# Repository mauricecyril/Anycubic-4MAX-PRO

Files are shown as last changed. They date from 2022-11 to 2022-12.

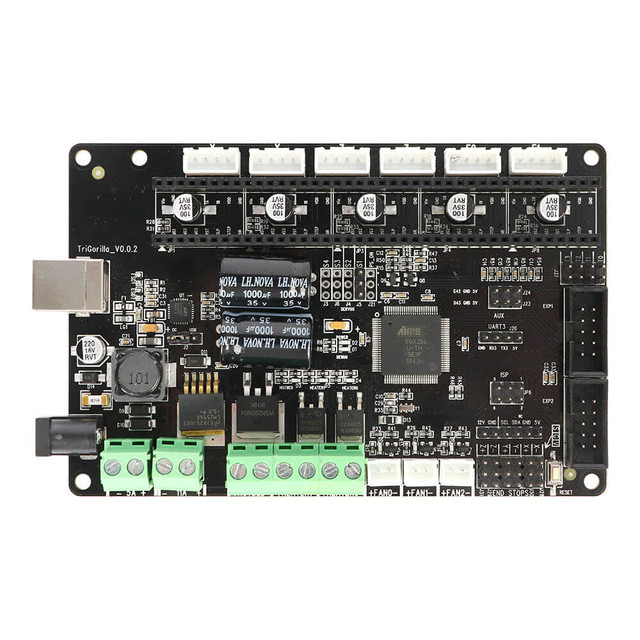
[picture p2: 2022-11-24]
references/anycubic-trigorilla-3d-printer-main-control-board-1000x1000__66155.jpg

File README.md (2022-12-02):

# Anycubic 4MAX PRO
Settings and Notes Related to the Anycubic 4Max Pro 3D Printer.

### **WARNING**: USE AT YOUR OWN RISK! All information collected on this github is for research purposes and is NOT professional advice or should not be considered a definative source for understanding, modifying or configuring the Anycubic 4Max Pro 3d printer or any 3d printer. Please do your own research and make sure you understand the potential risks, loss or damage to your health, your 3d printer, your house or those around you should you use the Anycubic 4Max Pro or follow or use any of the settings, files or information provided on this github repository. You assume all responsibility and liability for any damage or harm that may occur by following the information aggregated and posted here. USE AT YOUR OWN RISK!

## Information 
The heated bed of this printer tends to get warped and it becomes imposible to manually level the bed. The alternative is to add Mesh Leveling capabilities to this printer to make it usable.  

The printer uses a trigorilla board v1.0 but please double check by opening up the base of the printer and check the mainboard (see https://github.com/knutwurst/Marlin-2-0-x-Anycubic-i3-MEGA-S/wiki/Beginner's-Guide-(English)#3-identification-of-the-mainboard ) 

There is also a daughter board connected which has the pins for the end stops.

## Adding BL Touch to the Anycubic 4Max Pro V1.0
 **WARNING: USE AT YOUR OWN RISK! Please make sure to do your own configuration and conduct your own research before flashing your printers firmware, installing a BLTouch or configuring the BLtouch for the printer. I am not responsible for any potential risks, loss or damage to your health, your 3d printer, your house or those around you should you use the Anycubic 4Max Pro or follow or use any of the settings, files or information provided on this github repository. USE AT YOUR OWN RISK!**

### Purchase a genuine BLTouch
Try to acquire a genuine BLTouch device as there are reports of clones generally failing or having quality issues.
Make sure to also get the 1.5m extension wire with the dupont connectors.

The trigorilla mainboard on the Anycubic 4Max Pro has the servo control pins already soldered on
"+ - Power"
"- - GND"
"S - Signal"

But the BLTouch dupont connector needs to be reconfigured (see https://www.antclabs.com/wiring ) to swap the power and ground.
Original BLTouch Wiring 

| Original BLtouch Wiring | Modified BLtouch wiring | Connection to Anycubic 4MaxPro Boards |
| --- | --- |  --- |
| Brown (GND)  | Red (5V)  | + Servo Headers on Main Board |
| Red (5V)  | Brown (GND)  | - Servo Headers on Main Board |
| Orange (Signal)  | Orange (Signal)  | S Servo Headers on Main Board |
| Black (GND) | Black (GND)  | Black (GND) on Daughter board |
| White (Z axis Signal)  | White (Z axis Signal)  | White (Z axis Signal) on Daughter board  |

### Print a custom mount
Find a suitable BLtouch mount or experiment with one of the following:
| STL | Approximate Offset (Make sure to do your own calibration) | 
| --- | --- |
| Ancycubic 4MaxPro Standard Fan BLtouch Mount v4.stl | X Offset = +54.87mm, Y Offset = -1.70mm, Z Offset = |
| Ancycubic 4MaxPro Vortex Fan BLtouch Mount v2.stl | X Offset =+55.43mm , Y Offset =-2.0 (other readings say -7.91mm) , Z Offset = -3.58 or-3.52 (Probe extends 8.78mm - Distance from probe base to nozzle is 8.43mm). You might need to add a hex nut as a spacer to bring the probe lower. |

Make sure to calibrate the location of the BLTouch Probe in relation to your nozzle.

Remember the X,Y,Z are coordinates oriented when you're facing the front of the printer (ie. the door on the front of the 4Max Pro).
Y axis is the movement towards and away from you. So +Y is moving the printer head away from you, -Y is moving the printer head towards you.
X axis is the movement left and right of you. So +X is moving the printer head to the right, -X is moving the printer to the left.
Z axis is the movement up and down. So +Z is moving the pritner head up away from the printer bed, -Z is moving the printer down towards the printer bed.

### Flash the appropriate firmware (if required)
Knutwurst's i3 MEGA M/S/P/X/Chiron/4MP2 Hybrid Firmware (based on Marlin 2.1.x)
https://github.com/knutwurst/Marlin-2-0-x-Anycubic-i3-MEGA-S/releases

Make sure to compile your own version using the Arduino IDE and configure the X,Y,Z offsets! Make sure to follow the post firmware installation calibration steps. 

### Remove Bottom Cover
Lay the printer flat so that the bottom cover is exposed. To remove the base plate remove the four hex machine screws (M3x12) and also remove the padded covers and remove additional 4 machine hex screws (M4x8). 

### Remove Back Cover
Stand the printer back up (you can use the cover to protect the main board).
Remove the 8 screws on the back panel and remove the back panel to get run the extension cable through the existing cable management. You may want to add your own zip ties to anchor the new wires.

### Wire up the Extension Wire to the controller and daughter board
Lay the printer flat again (ie. front door laying flat).

# Ultimaker Cura 4.4 Settings for the Anycubic 4Max Pro
If "Origin at Center" is checked when slicing the printer seems to print off the printbed and in the lower left quadrant. Recommendation is to keep this setting unchecked. 

Settings / Printer / Manage Printers

Edit Machine Settings

Printer

    Printer Settings
    
        X (Width): 270mm
        Y (Depth): 205 mm
        Z (Height): 205 mm
        Build Plate Shape: Rectangular
        Origin at Center: Unchecked
        Heated Bed: Checked
        Heated Build Volume: Unchecked
        G-Code Flavor: Marlin
        
    Printhead Settings
        X min: 0
        Y min: 0
        X max: 205
        Y max: 205
        Gantry Height: 25.0
        Number of Extruders: 1
        
    Start G-Code
        G21 ;metric values
        G90 ;absolute positioning
        M82 ;set extruder to absolute mode
        M107 ;start with the fan off
        G28 X0 Y0 ;move X/Y to min endstops
        G28 Z0 ;move Z to min endstops
        G1 X-3 Y40 ;Anycubic 4Max Pro Brush
        G1 X-3 Y5 ;Anycubic 4Max Pro Brush
        G1 X-3 Y40 ;Anycubic 4Max Pro Brush
        G1 X-3 Y5 ;Anycubic 4Max Pro Brush
        G1 Z15.0 F{speed_travel} ;move the platform down 15mm
        G92 E0 ;zero the extruded length
        G1 F200 E3 ;extrude 3mm of feed stock
        G92 E0 ;zero the extruded length again
        G1 F{speed_travel}
        M117 Printing...
        G5

    End G-Code
        M104 S0 ; turn off extruder
        M140 S0 ; turn off bed
        M84 ; disable motors
        M107
        G91 ;relative positioning
        G1 E-1 F300 ;retract the filament a bit before lifting the nozzle, to release some of the pressure
        G1 Z+0.5 E-5 ;X-20 Y-20 F{speed_travel} ;move Z up a bit and retract filament even more
        G28 X0 ;Y0 ;move X/Y to min endstops, so the head is out of the way
        G1 Y180 F2000
        M84 ;steppers off
        G90
        M300 P300 S4000        

Extruder 1

    Nozzle Settings
    
        Nozzle Size: 0.4 mm
        Compatible Material Diameter: 1.75 mm
        Nozzle Offset X: 0 mm
        Nozzle Offset Y: 0 mm
        Cooling Fan Number: 0
        
    Extruder Start G-Code: Blank
    Extruder End G-Code: Blank
    
# Ultimaker Cura 4.4 Settings for the Anycubic 4Max Pro with BLTouch
If "Origin at Center" is checked when slicing the printer seems to print off the printbed and in the lower left quadrant. Recommendation is to keep this setting unchecked. Removed 

Settings / Printer / Manage Printers

Edit Machine Settings

Printer

    Printer Settings
    
        X (Width): 270mm
        Y (Depth): 205 mm
        Z (Height): 205 mm
        Build Plate Shape: Rectangular
        Origin at Center: Unchecked
        Heated Bed: Checked
        Heated Build Volume: Unchecked
        G-Code Flavor: Marlin
        
    Printhead Settings
        X min: 0
        Y min: 0
        X max: 205
        Y max: 205
        Gantry Height: 25.0
        Number of Extruders: 1
        
    Start G-Code
        G21 ;metric values
        G90 ;absolute positioning
        M82 ;set extruder to absolute mode
        M107 ;start with the fan off
        G28 X0 Y0 ;move X/Y to min endstops
        G28 Z0 ;move Z to min endstops
        G1 X-3 Y40 ;Anycubic 4Max Pro Brush
        G1 X-3 Y5 ;Anycubic 4Max Pro Brush
        G1 X-3 Y40 ;Anycubic 4Max Pro Brush
        G1 X-3 Y5 ;Anycubic 4Max Pro Brush
        G1 Z15.0 F{speed_travel} ;move the platform down 15mm
        G92 E0 ;zero the extruded length
        G1 F200 E3 ;extrude 3mm of feed stock
        G92 E0 ;zero the extruded length again
        G1 F{speed_travel}
        M117 Printing...
        G5

    End G-Code
        M104 S0 ; turn off extruder
        M140 S0 ; turn off bed
        M84 ; disable motors
        M107
        G91 ;relative positioning
        G1 E-1 F300 ;retract the filament a bit before lifting the nozzle, to release some of the pressure
        G1 Z+0.5 E-5 ;X-20 Y-20 F{speed_travel} ;move Z up a bit and retract filament even more
        G28 X0 ;Y0 ;move X/Y to min endstops, so the head is out of the way
        G1 Y180 F2000
        M84 ;steppers off
        G90
        M300 P300 S4000        

Extruder 1

    Nozzle Settings
    
        Nozzle Size: 0.4 mm
        Compatible Material Diameter: 1.75 mm
        Nozzle Offset X: 0 mm
        Nozzle Offset Y: 0 mm
        Cooling Fan Number: 0
        
    Extruder Start G-Code: Blank
    Extruder End G-Code: Blank

# Octoprint Settings
Still researching

# Sources

## Github
Knutwurst's i3 MEGA M/S/P/X/Chiron/4MP2 Hybrid Firmware (based on Marlin 2.1.x)
https://github.com/knutwurst/Marlin-2-0-x-Anycubic-i3-MEGA-S/releases

Marlin 2.0.x for Anycubic 4Max Pro [Does not compile in Arduino]
https://github.com/Poket-Jony/Marlin-A4MaxPro-2.0.x

## Thingiverse
Anycubic 4Max Pro Cable Chain by wadzio October 15, 2019
https://www.thingiverse.com/thing:3918237

Anycubic 4Max Pro Cable Chain - fixed parts by BgB42O June 14, 2020
https://www.thingiverse.com/thing:4459661

Vortex Fan Duct for Anycubic 4Max Pro by ontherunstudio July 26, 2019
https://www.thingiverse.com/thing:3772311

Anycubic 4Max Pro 2.0 Print head lid by alex_trask August 16, 2021
https://www.thingiverse.com/thing:4934115

4max pro Cura 4.1 profiles by skfinley July 29, 2019
https://www.thingiverse.com/thing:3778487

4Max Pro BLTouch Cable Holder by neutr0n January 07, 2020
https://www.thingiverse.com/thing:4090425

BLTouch and 3D Touch mount for Anycubic Mega S/X/P by Knutwurst October 25, 2021
https://www.thingiverse.com/thing:5030218

## Reddit
BLtouch on an Anycubic 4Max Pro by g8tto3
https://www.reddit.com/r/3Dprinting/comments/g8tto3/bltouch_on_an_anycubic_4max_pro/
https://web.archive.org/web/20221124154853/https://www.reddit.com/r/3Dprinting/comments/g8tto3/bltouch_on_an_anycubic_4max_pro/

BLTouch Installation (english) from Marlin-2-0-x-Anycubic-i3-MEGA-S
https://github.com/knutwurst/Marlin-2-0-x-Anycubic-i3-MEGA-S/wiki/BLTouch-Installation-(english)

Beginner's Guide (English) from Marlin-2-0-x-Anycubic-i3-MEGA-S
https://github.com/knutwurst/Marlin-2-0-x-Anycubic-i3-MEGA-S/wiki/Beginner's-Guide-(English)#3-identification-of-the-mainboard

Installed BLTouch last night. Here's things I wish I'd known.
https://www.reddit.com/r/ender3/comments/c6n02e/installed_bltouch_last_night_heres_things_i_wish/

Help me recognizing Trigorilla board versions
https://www.reddit.com/r/anycubic/comments/jns8l1/help_me_recognizing_trigorilla_board_versions/

## Other references
https://3dtoday.ru/blogs/darkcats/the-installation-of-the-level-sensor-table-bltouch3dtouch-and-clones-a

Camera Mounts to adapt:
https://www.thingiverse.com/thing:5147960

## Z - Offset Calibration
Source: https://github.com/knutwurst/Marlin-2-0-x-Anycubic-i3-MEGA-S/wiki/BLTouch-Installation-(english)
Also see: https://www.webcarpenter.com/blog/162-3D-Print---How-to-calibrate-Z-offset-with-a-BLTouch-bed-leveling-probe-sensor

Example:

Heat up the bed

G28

G90

G1 Z10

G1 X40 Y40 F4000

M280 P0 S10

G91

Slowly lower the nozzle with G1 Z-1 or G1 Z-0.1 or G1 Z-0.02 until the sensor is triggered. NOT FURTHER!

If the sensor has triggered and flashes: M280 P0 S160

M114 = Current position of the nozzle -> note! (e.g. Recv: X:40.00 Y:40.00 Z:1.30 E:0.00 Count X:3200 Y:3200 Z:520)

G90

G1 X38 Y15 F4000 (values from point 10 + offset of the sensor, i.e. X=40+(-2) and Y=40+(-25))

G91

Place a sheet of paper under the nozzle

Slowly lower the nozzle with G1 Z-1 or G1 Z-0.1 or G1 Z-0.02 until the paper is difficult to move.

M114 = Current position of the nozzle -> note! (e.g. Recv: X:38.00 Y:15.00 Z:0.70 E:0.00 Count X:3200 Y:3200 Z:520)

Subtract the Z value from point 16 from that from point 10 -> 1.30 - 0.7 = 0.6 mm -> This is our Z offset.

M851 Z-0.6 (be aware of the negative sign!)

M500

Carry out Autoleveling again via the display. Finished.

### Start G-Code - Cura
G21 ;metric values
G90 ;absolute positioning
M82 ;set extruder to absolute mode
M107 ;start with the fan off
M280 P0 S160 ; BLTouch alarm release
G4 P100 ; delay for BLTouch
G28 X0 Y0 ;move X/Y to min endstops
G28 Z0 ;move Z to min endstops
G28 ; home
G29 ; auto bed leveling
G1 X-3 Y40 ;Anycubic 4Max Pro Brush
G1 X-3 Y5 ;Anycubic 4Max Pro Brush
G1 X-3 Y40 ;Anycubic 4Max Pro Brush
G1 X-3 Y5 ;Anycubic 4Max Pro Brush
G1 Z15.0 F{speed_travel} ;move the platform down 15mm
G92 E0 ;zero the extruded length
G1 F200 E3 ;extrude 3mm of feed stock
G92 E0 ;zero the extruded length again
G1 F{speed_travel}
M117 Printing...
G5

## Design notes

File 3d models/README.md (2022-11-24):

# Slicer Settings

Use PETG or a heat resistant material. 

In tests, I've used Overture Black PETG and there was some stringing that needed cleaning up after. 

## Ultimaker Cura Settings

### Layer Height, Infill, Temp
Layer Height: 0.15mm

Infill Density: 100%

Print Temperature: 250.0 C

Build Plate Temperature: 70.0 C

### Cooling
Enable Print Cooling: No

Regular/Maximum Fan Speet Threshold: 10%

Regular Fan Speed at Height: 0.3mm

Regular Fan Speed at Layer: 2

Minimum Layer Time: 5.0s

Minimum Speed: 10.0 mm/s

Lift Head: No

### Supports
Generate Supports: Yes

Support Structure: Normal

Support Placement: Touching Buildplate

Support Overhang Angle: 50%

Support Pattern: Lines

Support Density: 15%

### Adhesion
Build Plate Adhesion: Yes

Build Plate Adhesion Type: Skirt

Skirt Line Couunt: 1

Skirt Distance 3.0mm

Skirt/Brim Minimum Length: 250.0mm

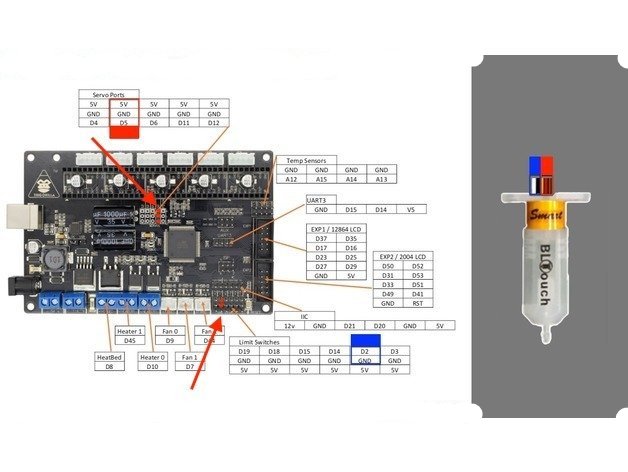
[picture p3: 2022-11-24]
references/trigorilla board bltouch.jpg

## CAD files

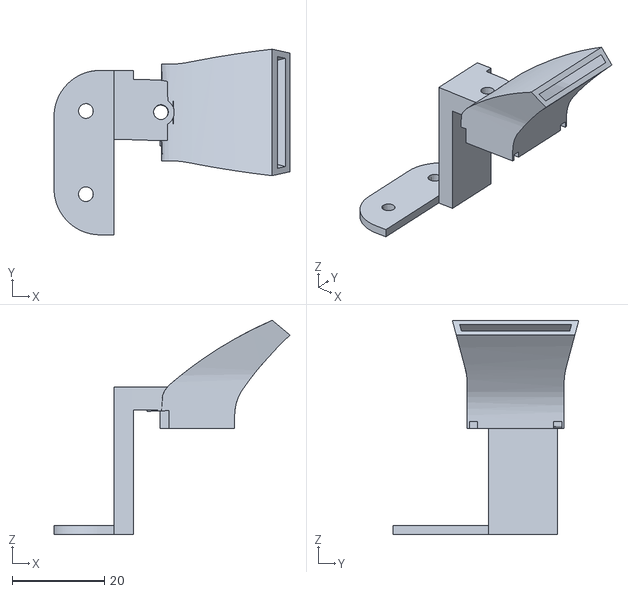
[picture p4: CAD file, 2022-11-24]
3d models/Ancycubic 4MaxPro Standard Fan BLtouch Mount v4.stl
51.1 x 40.2 x 46.4

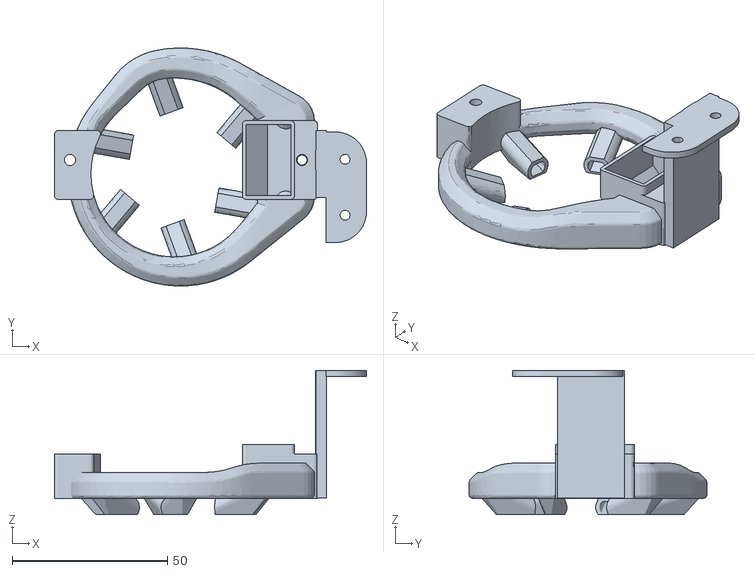
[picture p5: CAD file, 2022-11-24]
3d models/Ancycubic 4MaxPro Vortex Fan BLtouch Mount v2.stl
100.5 x 76.7 x 46.5

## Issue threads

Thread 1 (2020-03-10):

should the x max be 270 rather than 205?

mrantonwinter, 2020-03-10:
Printhead Settings
    X max: 270

or does it only go to 205?

pieterbritz, 2020-04-18:
Printer Settings should be:
X max = 205mm
Y max = 205mm
Z max = 270mm

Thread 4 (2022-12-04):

z offset value

FTHSONE, 2022-12-04:
Missing Anycubic 4MaxPro Standard Fan BLtouch Mount v4.stl  Z offset value

Closed 2022-12-07.

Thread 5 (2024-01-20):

Power

john-clark, 2024-01-20:
Do you use Octoprint? How do you power on the printer remotely?

SvenMb, 2024-05-09:
unfortunately this is not possible. the power relay inside the 4Max pro printer can not be switched via G-code.

I just removed it and switch the printer via external tasmota relay and PSU Control Tasmota in octoprint.

john-clark, 2024-05-27:
Can you show what you did?
